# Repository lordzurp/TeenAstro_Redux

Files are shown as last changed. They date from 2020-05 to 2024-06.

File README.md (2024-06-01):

# TeenAstro Redux Project
#### a mini version of the TeenAstro mini version
=========================

## Project moved !
please visit my new repo : [zUrp Astronomics/Unicorn](https://github.com/zUrp-Astronomics/unicorn)

## License
GPL v3

## Author
lordzurp
based on great work of [Charles Lemaire](https://github.com/charleslemaire0/TeenAstro) and [Howard Dutton](http://www.stellarjourney.com) (and a lot of contributors)

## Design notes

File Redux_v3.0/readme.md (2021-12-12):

# TeenAstro Redux Project

#### A mini version of the TeenAstro mini

[][release]
[][license] 

[release]: https://github.com/lordzurp/TeenAstro_Redux/releases
[license]: https://raw.githubusercontent.com/lordzurp/TeenAstro_Redux/master/LICENSE

===========================

## Redux 3.0 — the Finale Edition

### Pre-release notes

> The board isn’t validated yet, please don’t build it right now! Also, the firmware isn’t final neither.

===========================

This version is a mix between the main board and the mini board. The idea is to have a (very) small board that can easily integrate with mounts while still retaining the extended functions of the main unit.

## Source files
[EasyEDA](https://oshwlab.com/lordzurp/teenastro-redux_v3)

## 3D view

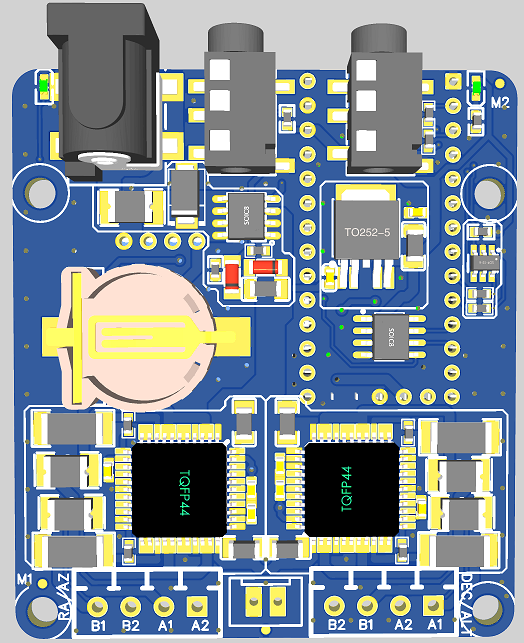
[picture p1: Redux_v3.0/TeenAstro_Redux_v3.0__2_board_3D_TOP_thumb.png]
3D_top

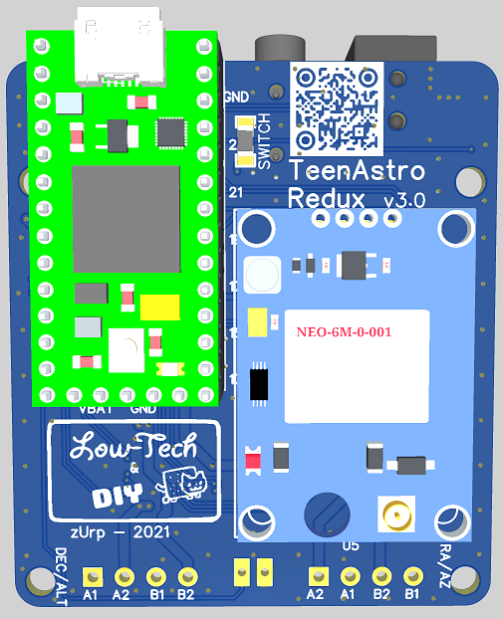
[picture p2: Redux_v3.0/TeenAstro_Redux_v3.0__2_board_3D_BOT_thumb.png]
3D_bot


## Schematics

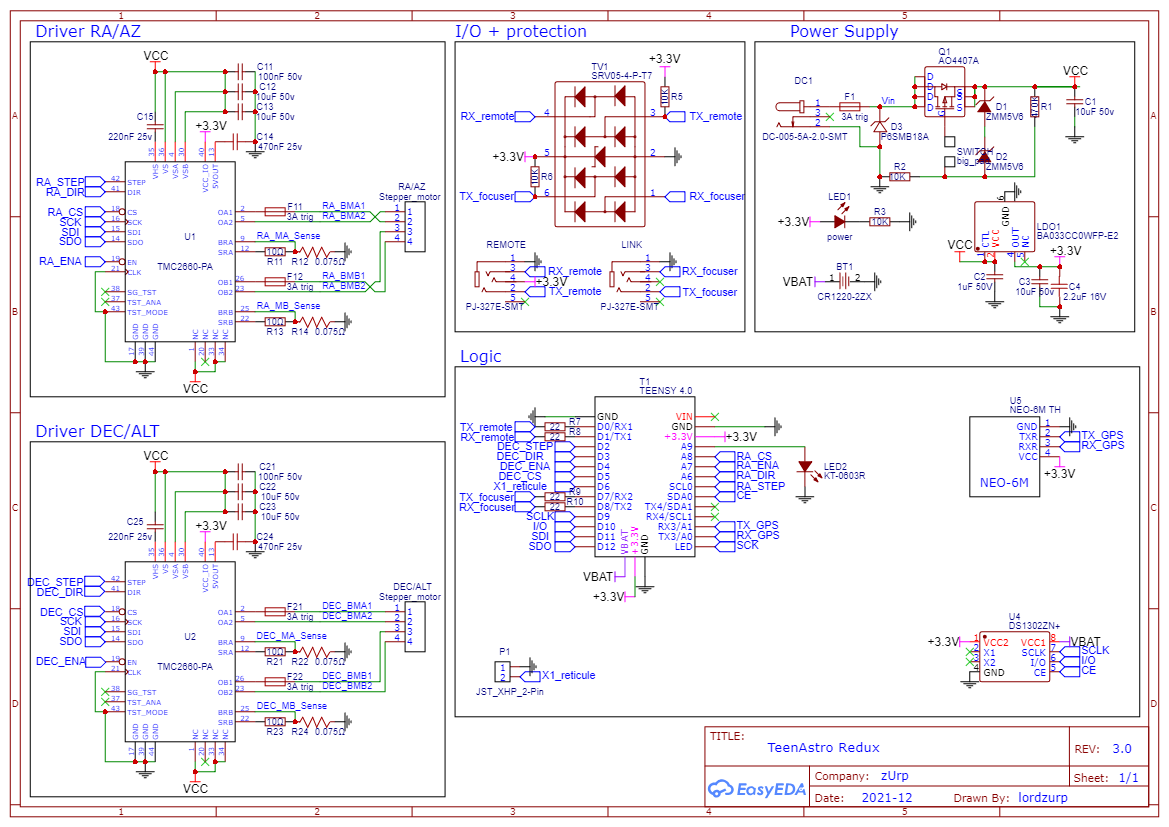
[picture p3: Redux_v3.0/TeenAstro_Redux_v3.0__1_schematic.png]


## Evolution from the v2.4 series

### Teensy 4.0
The (not so) new Teensy 4.0 is a beast of computing power, with a 600 MHz Cortex-M7 CPU. It is almost pin-to-pin compatible with the Teensy 3.2, except for the UART.

The main difference is that the 4.0 **isn’t 5 V compliant**, the logic voltage is 3.3 V across the board and the SHC.

The board’s routing was updated to comply with the constraints of the new form factor. As a consequence, specific firmware is needed, with branch 3.0 (under development).

### Integrated Stepper Driver
To minimize the assembling complexity of the unit, the motor drivers are soldered directly to the board. This makes for more reliable connections and easier production.

The chosen drivers are the **TMC2660**.

They include all the benefits and internal functions of the TMC5160, but with integrated MOSfet which is capable of driving the 3A max stepper motors and is protected by resetting fuses.

### Onboard GPS
There is a space on the board to solder a GPS module.

Depending on the casing, you may need an external antenna (if there’s not enough place inside, or if the casing is made of metal which would reduce the gain of the antenna).

### Focuser
**Awaiting software development**

The board can be used either to control the mount or the focuser or the derotator. The onboard additional chip (DS1302) can be used by the focuser’s firmware and ignored by the main firmware.

A link port allows connecting the two boards and it also provides unified controls with a crossover cable. The use depends on which firmware is uploaded to the board.

### Reworked Power Supply
The power input is protected from polarity inversion, ESD and short-circuiting by a resetting 3A fuse.

The ON/OFF switch is now a logic-level switch, it doesn’t have to support the full-board current. Any regular switch will do the job. Two pads are added for soldering the wires and one can short-circuit them if there is no need for a power-off switch.

The logic voltage is **3.3 V**, as per the Teensy 4.0 requirements (see below).

The button battery is now a CR1220 (standard CR2032 is far too big).

### Protected I/O
The SHC port and the link port are ESD-protected, so you can plug them while the board is ON (although this isn’t recommended…).

### Removed Features
*	no ST4 port anymore: since the mount guiding requires a computer, having only the USB_link option shouldn’t be a problem.

## Firmware and software update needed (WiP)
*	new pinout
*	TMC2660 support
*	Uploader and Config tool, to support new branch
*	additional motor on the focuser: can be used for a secondary focuser or derotator. Some code is available in OnStep, need to review and merge
*	INDI driver: unified control of mount and focuser with a single USB link

## Production Notes
**Follows JLCpcb Capabilities**

*	2-layer board
*	Min track width: 0.2 mm
*	Min clearance: 0.2 mm
*	Via size: 0.25/0.5 mm

#### SMD parts
The whole SMD parts are sourced from the JLCpcb assembly list, so you can order a fully SMD-assembled board.

#### Additional parts
*	Teensy 4.0
*	GPS module (neo-6 compatible)
*	Motor connectors (4 ways pitch 3.5 mm or wires)
*	ON/OFF switch (optional)
*	Reticule connector (optional)

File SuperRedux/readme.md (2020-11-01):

# TeenAstro Redux Project
#### a mini version of the TeenAstro mini version
===========================

## SuperRedux 2.5 - the Small One

### Production notes

**Follow JLCpcb capabilities**

* 4-layers board
* Min track width : 0.15mm
* Min clearence : 0.13mm
* Via size : 0.25/0.5mm

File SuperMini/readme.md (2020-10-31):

## Production notes

**Follow JLCpcb capabilities**

* double-layer board
* Min track width : 0.2mm
* Min clearence : 0.15mm
* Via size : 0.25/0.5mm

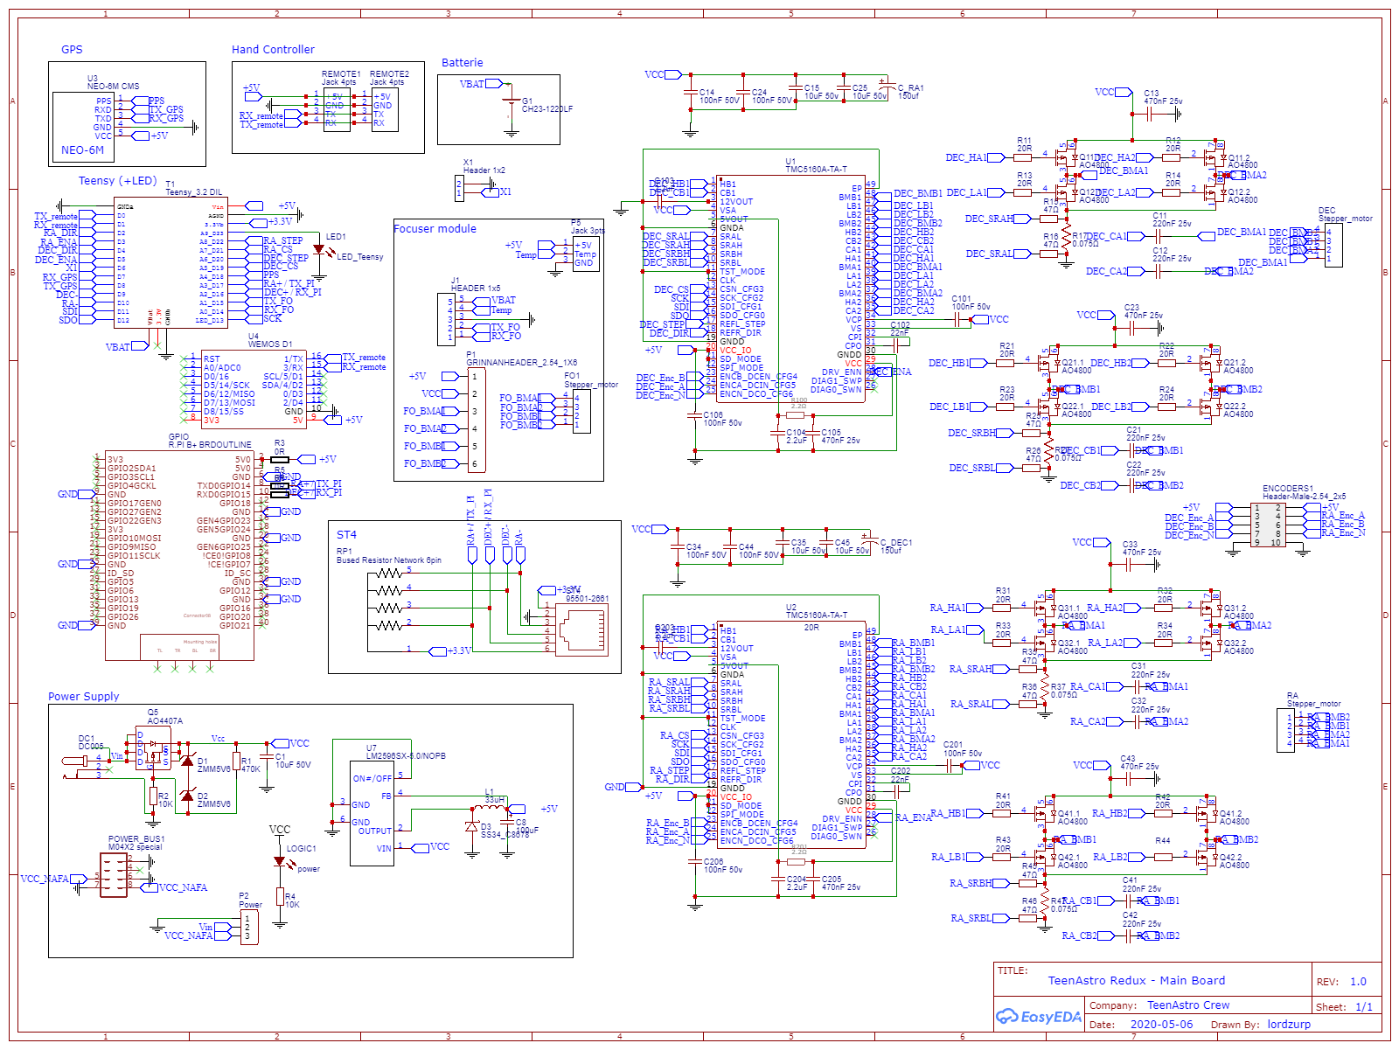
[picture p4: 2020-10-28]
Schematic_TeenAstro SuperMini - PI Edition copy +5v_2020-10-26_22-45-55.png

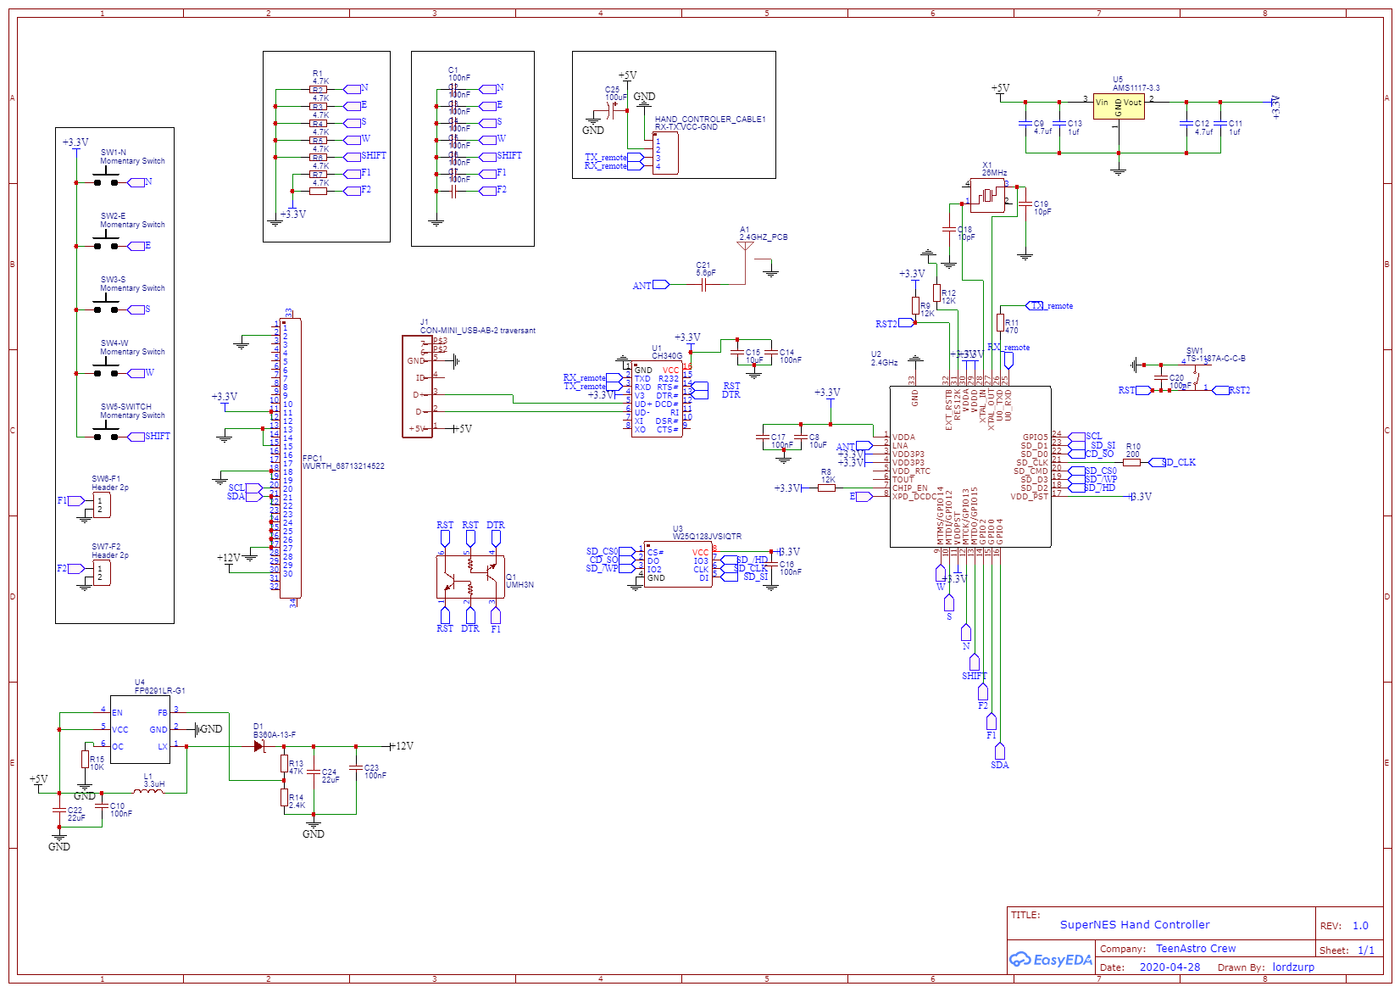
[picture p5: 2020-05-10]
Schematics/Hand_controller.png

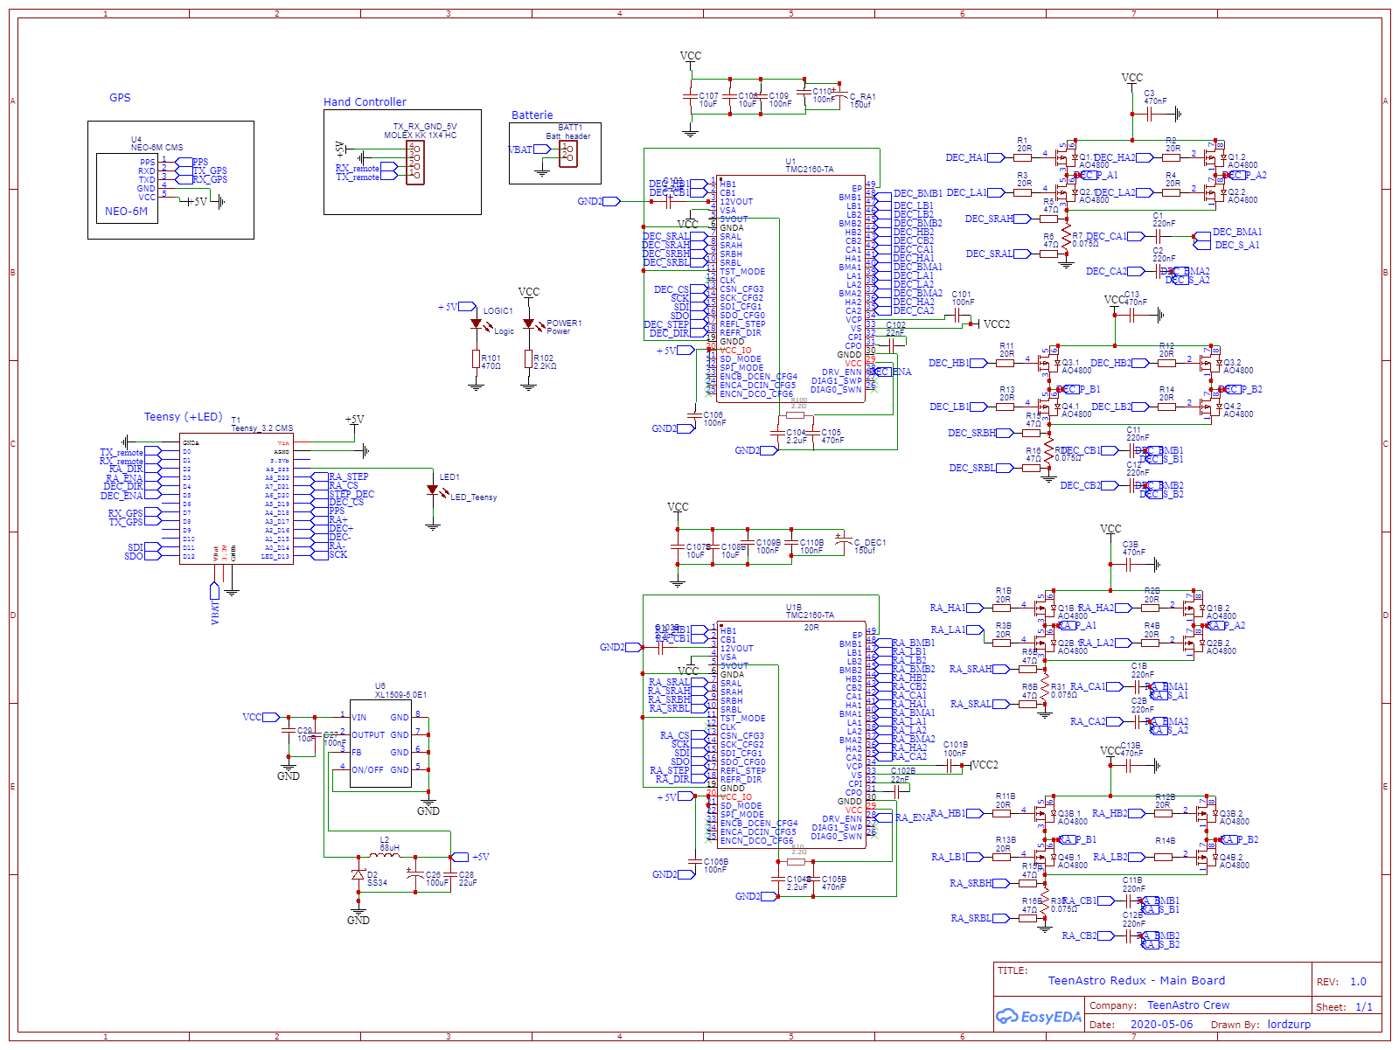
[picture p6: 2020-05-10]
Schematics/Main_board.png

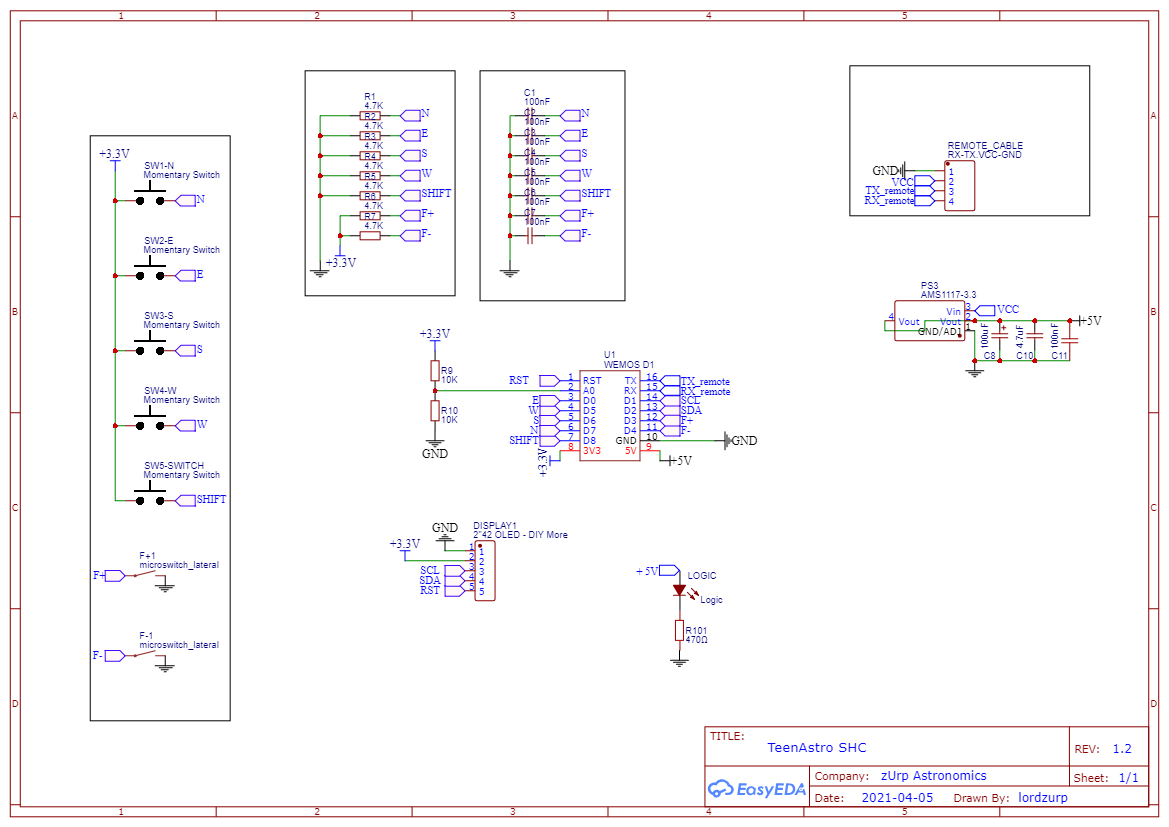
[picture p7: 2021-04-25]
hand controller/TeenAstro SHC - 1_schematic.png

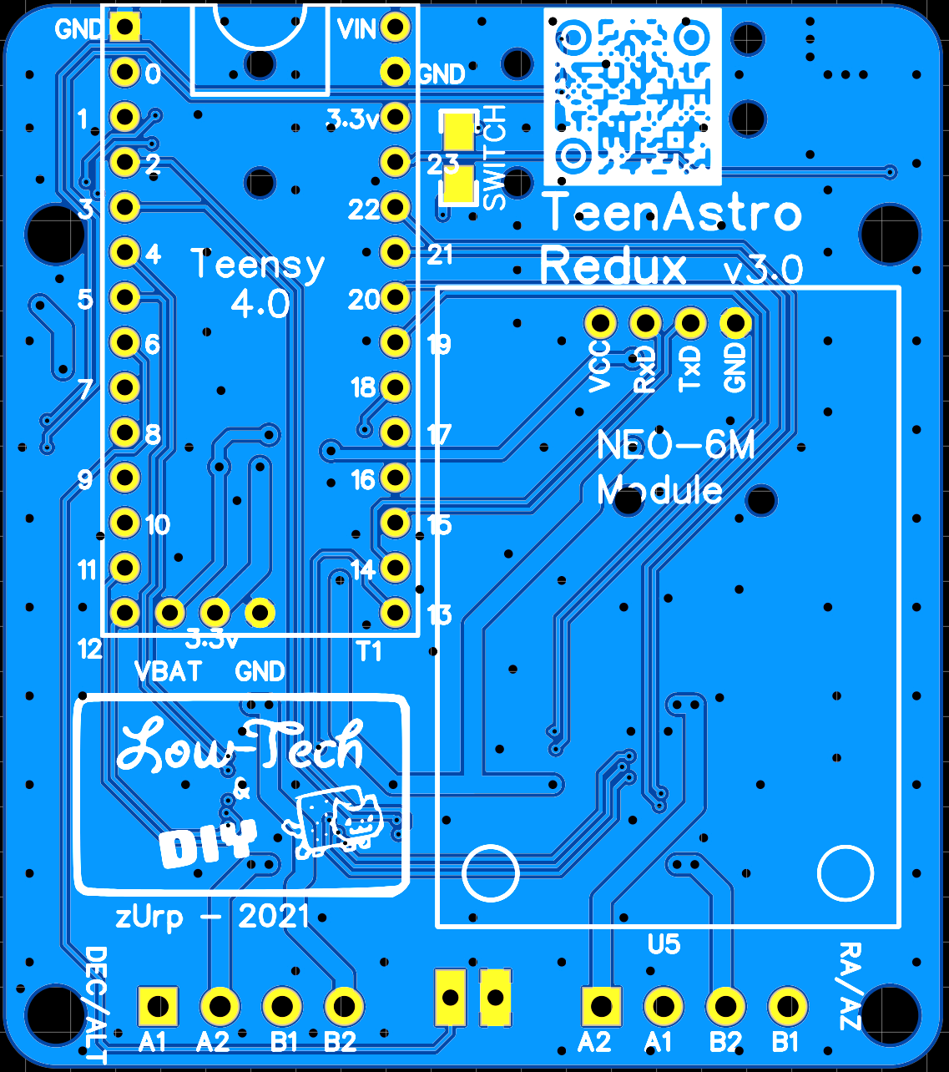
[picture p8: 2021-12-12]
Redux_v3.0/TeenAstro_Redux_v3.0__2_board_BOT.png

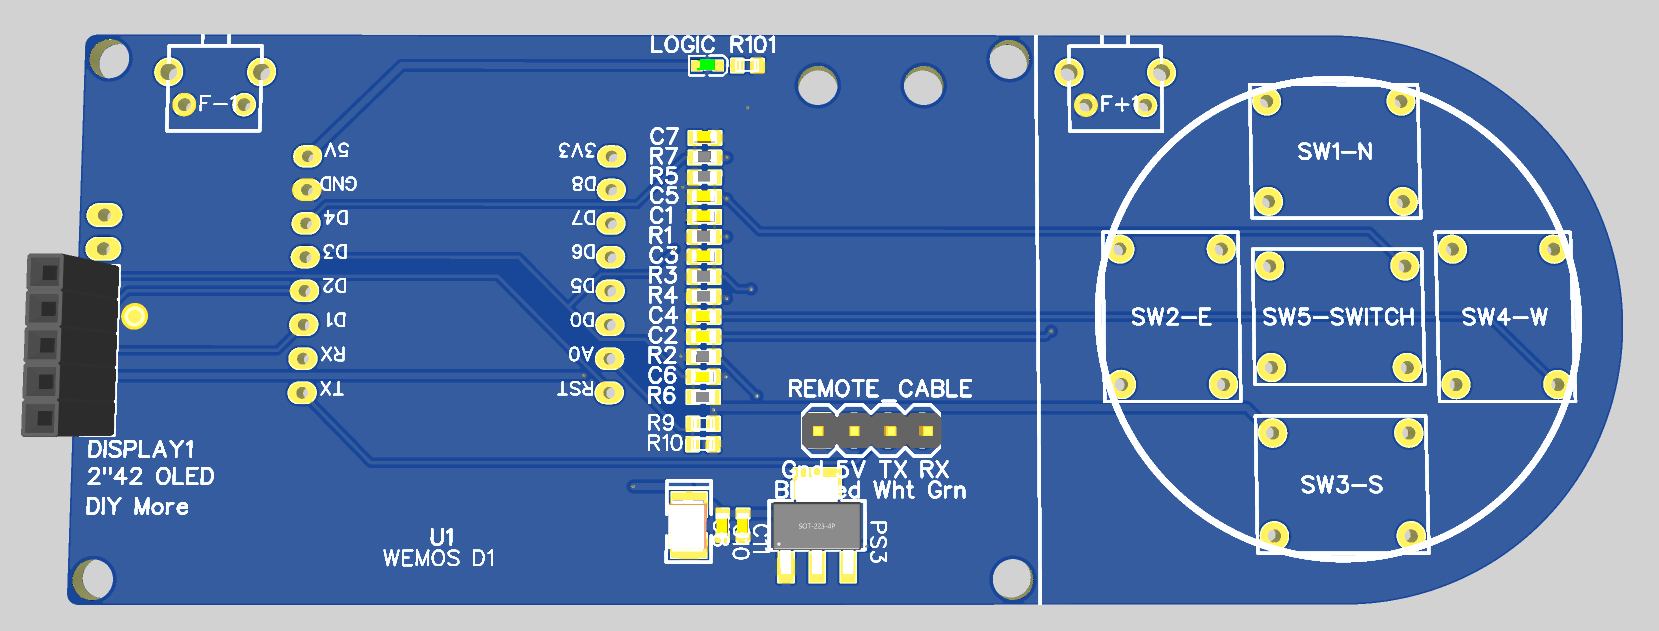
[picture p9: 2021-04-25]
hand controller/TeenAstro SHC - 2_3D-view.png

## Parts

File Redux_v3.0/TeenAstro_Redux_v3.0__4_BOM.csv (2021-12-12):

ID | Name | Designator | Footprint | Quantity | Manufacturer Part | Manufacturer | Supplier | Supplier Part | Price
1 | CR1220-2ZX | BT1 | BAT-SMD_CR1220-2ZX | 1 | CR1220-2ZX | Q&J | LCSC | C969906 | 0.283
2 | 10uF 50v | C1,C3,C12,C13,C22,C23 | C1206 | 6 | CL31A106KBHNNNE | SAMSUNG | LCSC | C13585 | 0.033
3 | 1uF 50V | C2 | C0603 | 1 | CL10A105KB8NNNC | SAMSUNG | LCSC | C15849 | 0.005
4 | 2.2uF 16V | C4 | C_0603 | 1 | CL10A225KO8NNNC | SAMSUNG | LCSC | C23630 | 0.006
5 | 100nF 50v | C11,C21 | C_0603 | 2 | CC0603KRX7R9BB104 | YAGEO | LCSC | C14663 | 0.002
6 | 470nF 25v | C14,C24 | C_0603 | 2 | CL10B474KA8NNNC | SAMSUNG | LCSC | C1623 | 0.007
7 | 220nF 25v | C15,C25 | C_0603 | 2 | CL10B224KA8NNNC | SAMSUNG | LCSC | C21120 | 0.006
8 | ZMM5V6 | D1,D2 | LL-34_L3.5-W1.5-RD | 2 | ZMM5V6 | SEMTECH | LCSC | C8062 | 0.017
9 | P6SMB18A | D3 | SMB_L4.6-W3.6-LS5.3-RD | 1 | P6SMB18A | Formosa Microsemi | LCSC | C286254 | 0.056
10 | DC-005-5A-2.0-SMT | DC1 | DC-IN-TH_DC-005-5A-2.0-SMT | 1 | DC-005-5A-2.0-SMT | XKB Enterprise | LCSC | C319134 | 0.177
11 | Stepper_motor | DEC/ALT,RA/AZ | STEPPER_MOTOR_VERT | 2 | 1x4 pin header
12 | 3A trig | F1,F11,F12,F21,F22 | F1812 | 5 | SMD1812P300SLR/24 | PTTC(Polytronics Tech) | LCSC | C495359 | 0.464
13 | BA033CC0WFP-E2 | LDO1 | TO-252-5_L6.5-W5.5-P1.30-LS10.0-BR | 1 | BA033CC0WFP-E2 | ROHM | LCSC | C84986 | 0.808
14 | power | LED1 | LED0603-R-RD | 1 | 19-217/GHC-YR1S2/3T | EVERLIGHT | LCSC | C72043 | 0.027
15 | KT-0603R | LED2 | LED0603-R-RD | 1 | KT-0603R | KENTO | LCSC | C2286 | 0.005
16 | PJ-327E-SMT | LINK,REMOTE | AUDIO-SMD_PJ-327E-SMT | 2 | PJ-327E-SMT | XKB Enterprise | LCSC | C319105 | 0.118
17 | JST_XHP_2-Pin | P1 | JST-XHP2 | 1
18 | AO4407A | Q1 | SOIC-8_L4.9-W3.9-P1.27-LS6.0-BL | 1 | AO4407A | AOS | LCSC | C2841482 | 0.199
19 | 470K | R1 | R0603 | 1 | 0603WAF4703T5E | UniOhm | LCSC | C23178 | 0.001
20 | 10K | R2,R3,R5,R6 | R0603 | 4 | 0603WAF1002T5E | UniOhm | LCSC | C25804 | 0.001
21 | 22 | R7,R8,R9,R10 | R0603 | 4 | 0603WAF220JT5E | UniOhm | LCSC | C23345 | 0.001
22 | 10Ω | R11,R13,R21,R23 | R0603 | 4 | 0603WAF100JT5E | UniOhm | LCSC | C22859 | 0.001
23 | 0.075Ω | R12,R14,R22,R24 | R2512 | 4 | MS123WF750MT4E | Uniroyal Elec | LCSC | C78195 | 0.126
24 | big_pad | SWITCH | BIG_PAD | 1 |  |  | PJRC
25 | TEENSY 4.0 | T1 | TEENSY 4.0 DIL | 1 | Teensy 4.0 | PJRC
26 | SRV05-4-P-T7 | TV1 | SOT-23-6_L2.9-W1.6-P0.95-LS2.8-BR | 1 | SRV05-4-P-T7 | PROTEK | LCSC | C85364 | 0.125
27 | TMC2660-PA | U1,U2 | PQFP44_WITH_PADS | 2 | TMC2660-PA-T | Trinamic | LCSC | C915852 | 9.548
28 | DS1302ZN+ | U4 | SOIC-8_L4.9-W3.9-P1.27-LS6.0-BL | 1 | DS1302Z+T&R | MAXIM | LCSC | C8959 | 4.07
29 | NEO-6M TH | U5 | NEO-6M-GPS TH | 1 | NEO-6M |  | PJRC

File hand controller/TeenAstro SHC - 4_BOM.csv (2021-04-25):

ID | Name | Designator | Footprint | Quantity | Manufacturer Part | Manufacturer | Supplier | Supplier Part | Price | LCSC Assembly | JLCPCB SMD | Paste Type
1 | 100nF | C1,C2,C3,C4,C5,C6,C7,C11 | C_0603 | 8 | CC0603KRX7R9BB104 | YAGEO | LCSC | C14663 | 0.0034 | Yes
2 | 100uF | C8 | CAP-SMD_L3.5-W2.8 | 1 | TAJB107K006RNJ | AVX | LCSC | C16133 | 0.1544 | Yes | Yes | base
3 | 4.7uF | C10 | C_0603 | 1 | CL10A475KO8NNNC | SAMSUNG | LCSC | C19666 | 0.0132 |  | Yes
4 | 2"42 OLED - DIY More | DISPLAY1 | HDR-TH_5P-P2.54-V | 1 | 2.54mm 1*5P Header | ReliaPro | LCSC | C50951 | 0.0161
5 | microswitch_lateral | F+1,F-1 | MICROSWITCH_LATERAL | 2
6 | Logic | LOGIC | LED0603-RD | 1 | 19-217/GHC-YR1S2/3T | EVERLIGHT | LCSC | C72043 | 0.0246 | Yes
7 | AMS1117-3.3 | PS3 | SOT-223-3_L6.5-W3.4-P2.30-LS7.0-BR | 1 | AMS1117-3.3 | AMS | LCSC | C6186 | 0.0998 | Yes | Yes | base
8 | 4.7K | R1,R2,R3,R4,R5,R6,R7 | R_0603 | 7 | 0603WAF4701T5E | UniOhm | LCSC | C23162 | 0.0012 | Yes
9 | 10K | R9,R10 | R_0603 | 2 | 0603WAF1002T5E | UniOhm | LCSC | C25804 | 0.001 | Yes | Yes | base
10 | 470Ω | R101 | R_0603 | 1 | 0603WAF4700T5E | UniOhm | LCSC | C23179 | 0.0014 | Yes
11 | RX-TX.VCC-GND | REMOTE_CABLE | HDR-TH_4P-P2.54-V_LARGE | 1 | 210S-1*4P L=11.6MMGold-plated black | Ckmtw | LCSC | C124378 | 0.0261 | Yes |  | expand
12 | Momentary Switch | SW1-N,SW2-E,SW3-S,SW4-W,SW5-SWITCH | SWITCH_NAVI | 5 | TL3300CF260Q | E-SWITCH | Mouser | 612-TL3300CF260Q
13 | WEMOS D1 | U1 | WEMOS D1 MINI | 1

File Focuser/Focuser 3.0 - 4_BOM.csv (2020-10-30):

ID | Name | Designator | Footprint | Quantity | Manufacturer Part | Manufacturer | Supplier | Supplier Part | LCSC Assembly
1 | Momentary Switch | SW1-N,SW5-SWITCH,SW4-W,SW3-S,SW2-E | SWITCH_NAVI | 5 | TL3300CF260Q | E-SWITCH | Mouser | 612-TL3300CF260Q
2 | Header 2p | SW7-F2,SW6-F1 | HDR-TH_2P-P2.54-V-M | 2 | 2.54-1*2PFemale | BOOMELE | LCSC | C49661
3 | 4.7K | R5,R6,R1,R2,R3,R4,R7 | R_0603 | 7 | 0603WAF4701T5E | UniOhm | LCSC | C23162 | Yes
4 | 470Ω | R101 | R_0603 | 1 | 0603WAF4700T5E | UniOhm | LCSC | C23179 | Yes
5 | 100nF | C6,C5,C4,C3,C2,C1,C7 | C_0603 | 7 | CC0603KRX7R9BB104 | YAGEO | LCSC | C14663 | Yes
6 | 2.54mm 1*5P Header | P1 | HDR-TH_5P-P2.54-V | 1 | 2.54mm 1*5P Header | ReliaPro | LCSC | C50951
7 | Logic | LOGIC1 | LED0603-RD | 1 | 19-217/GHC-YR1S2/3T | EVERLIGHT | LCSC | C72043 | Yes
8 | RX-TX.VCC-GND | HAND_CONTROLER_CABLE1 | 210S-1X4P | 1 | 210S-1*4P L=11.6MMGold-plated black | Ckmtw | LCSC | C124378
9 | WEMOS D1 | U2 | WEMOS D1 MINI | 1
10 | 100uF | C9 | CAP-SMD_L3.5-W2.8-R-RD | 1 | TAJB107K006RNJ | AVX | LCSC | C16133 | Yes

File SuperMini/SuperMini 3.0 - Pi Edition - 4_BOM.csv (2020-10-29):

ID | Name | Designator | Footprint | Quantity | Manufacturer Part | Manufacturer | Supplier | Supplier Part | LCSC Assembly | Mounted | EasyEDA
1 | 2.2Ω | R100,R201 | R_0603 | 2 | 0603WAF220KT5E | UniOhm | LCSC | C22939
2 | 0.075Ω | R47,R37,R27,R17 | R2512 | 4 | MS123WF750MT4E | Uniroyal Elec | LCSC | C78195
3 | SS34_C8678 | D3 | DO-214AC_L4.3-W2.7-LS5.3-RD | 1 | SS34 | MDD | LCSC | C8678 | Yes
4 | 33uH | L1 | IND-SMD_L7.1-W6.6_YXMAA0603 | 1 | MWSA0603-330MT | Sunlord | LCSC | C132138 | Yes
5 | M04X2 special | POWER_BUS1 | HDR-M-2.54_2X4 SPECIAL | 1
6 | ZMM5V6 | D1,D2 | LL-34_L3.5-W1.5-RD | 2 | ZMM5V6 | SEMTECH | LCSC | C8062 | Yes
7 | Teensy_3.2 DIL | T1 | TEENSY 4.0 DIL | 1 | Teensy 3.2 |  | PJRC | TEENSY32 |  | Yes
8 | WEMOS D1 | U4 | WEMOS_D1_MINI_LIGHT | 1
9 | NEO-6M CMS | U3 | GPS NEO-6M | 1 | NEO-6M |  | PJRC
10 | 470K | R1 | R0805 | 1 | 0805W8F4703T5E | UniOhm | LCSC | C17709 | Yes
11 | LM2596SX-5.0/NOPB | U7 | TO-263-5_L10.2-W9.9-P1.70-LS14.4-TL | 1 | LM2596SX-5.0/NOPB | TI | LCSC | C10002 | Yes
12 | CH23-1220LF | G1 | CH23-1220LF | 1
13 | Header 2.54 1X6 | P1 | HEADER_2.54_1X6_PCB | 1 | Header-Male-2.54_1x6 | BOOMELE |  | C37208
14 | AO4407A | Q9 | SOIC-8_L4.9-W3.9-P1.27-LS6.0-BL | 1 | AO4407A | AOS | LCSC | C16072 | Yes
15 | 22nF | C202,C102 | C_0603 | 2 | CL10B223KB8NNNC | SAMSUNG | LCSC | C21122 | Yes
16 | Jack 3pts | P5 | JACK_3.5_3PTS | 1 | Molex_4x1
17 | 100nF 50V | C14,C34,C44,C24 | C0603 | 4 | CC0603KRX7R9BB104 | YAGEO | LCSC | C14663 | Yes
18 | power | LOGIC1 | LED0603-RD | 1 | 19-217/GHC-YR1S2/3T | EVERLIGHT | LCSC | C72043 | Yes
19 | LED_Teensy | LED1 | LED0603-RD | 1 | 19-217/GHC-YR1S2/3T | EVERLIGHT | LCSC | C72043 | Yes
20 | 0R | R5,R6,R3 | R0805_SHORT | 3
21 | Bused Resistor Network 6pin | RP1 | RESSIP-5 | 1 | Bused Resistor Network 6pin
22 | 95501-2661 | ST4 | 85503-5001 | 1 | 95501-2661 | MOLEX | LCSC | C240856
23 | 470nF 25v | C33,C205,C23,C13,C105,C43 | C_0603 | 6 | CL10B474KA8NNNC | SAMSUNG | LCSC | C1623 | Yes
24 | 150uf | C_DEC1,C_RA1 | 100UF/25V | 2 | ?
25 | 10uF 50v | C15,C25,C35,C45 | C1206 | 4 | CL31A106KBHNNNE | SAMSUNG | LCSC | C13585 | Yes
26 | 10uF 50V | C1 | C1206 | 1 | CL31A106KBHNNNE | SAMSUNG | LCSC | C13585 | Yes
27 | DC005 | DC1 | DC-IN-TH_DC-005-5A-2.0 | 1 | - | Made in China | LCSC | C9738
28 | TMC5160A-TA-T | U2,U1 | TQFP-48_L7.0-W7.0-P0.50-LS9.0-BL-EP | 2 | TMC2160-TA-T | TRINAMIC Motion Control GmbH | LCSC | C465948 | Yes
29 | Stepper_motor | DEC1,RA1,FO1 | STEPPER_MOTOR | 3 | 1x4 pin header
30 | 10K | R4 | R0603 | 1 | 0603WAF1002T5E | UniOhm | LCSC | C25804 | Yes
31 | SMD1812P300SLR/24 | F4,F3,F2,F1,F6,F5 | F1812 | 6 | SMD1812P300SLR/24 | PTTC(Polytronics Tech) | LCSC | C495359 | Yes
32 | 100uF | C8 | CAP-SMD_L3.5-W2.8-R-RD | 1 | TAJB107K006RNJ | AVX | LCSC | C16133 | Yes
33 | HEADER 1x5 | J1 | 1X5-2.54MM-HEADER | 1
34 | Power | P2 | HDR-TH_3P-P2.54-V | 1 | Header-Female-2.54_1x3 | Boom Precision Elec | LCSC | C146243
35 | 2.2uF | C103,C104,C204,C203 | C_0603 | 4 | CL10A225KO8NNNC | SAMSUNG | LCSC | C23630 | Yes
36 | Header 1x2 | X1 | HEADER 1X2 | 1
37 | 100nF 50v | C206,C101,C201,C106 | C_0603 | 4 | CC0603KRX7R9BB104 | YAGEO | LCSC | C14663 | Yes
38 | 10K | R2 | R0805 | 1 | 0805W8F1002T5E | UniOhm | LCSC | C17414 | Yes
39 | R.PI B+ BRDOUTLINE | GPIO1 | RASPBERRY PI 3 B+ | 1
40 | 47Ω | R46,R45,R25,R26,R16,R35,R15,R36 | R_0603 | 8 | 0603WAF470JT5E | UniOhm | LCSC | C23182 | Yes
41 | 220nF 25v | C42,C41,C32,C31,C22,C21,C11,C12 | C_0603 | 8 | CL10B224KA8NNNC | SAMSUNG | LCSC | C21120 | Yes
42 | 20R | R31,R43,R41,R14,R24,R11,R22,R21,R33,R32,R34,R44,R42,R23,R13,R12 | R_0603 | 16 | 0603WAF200JT5E | UniOhm | LCSC | C22950 | Yes
43 | Jack 4pts | REMOTE2,REMOTE1 | JACK_3.5_4PTS | 2 | Molex_4x1
44 | Header-Male-2.54_2x5 | ENCODERS1 | HDR-5X2/2.54 | 1 | Header-Male-2.54_2x5 | EasyEDA | EasyEDA | E28207 |  |  | E28207
45 | AO4800 | Q8,Q4,Q7,Q1,Q2,Q3,Q5,Q6,Q32,Q11,Q12,Q41,Q42,Q31,Q22,Q21 | SOIC-8_L4.9-W3.9-P1.27-LS6.0-BL | 16 | AO4800 | AOS | LCSC | C17098

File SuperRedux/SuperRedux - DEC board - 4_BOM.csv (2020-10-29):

ID | Name | Designator | Footprint | Quantity | Manufacturer Part | Manufacturer | Supplier | Supplier Part | Mounted | LCSC Assembly
1 | 2.2Ω | R201 | R_0603 | 1 | 0603WAF220KT5E | UniOhm | LCSC | C22939
2 | 0.075Ω | R47,R37 | R2512 | 2 | MS123WF750MT4E | Uniroyal Elec | LCSC | C78195
3 | Teensy_3.2 CMS | T1 | TEENSY 3.2 DIL | 1 | Teensy 3.2 |  | PJRC | TEENSY32 | Yes
4 | 22nF | C202 | C_0603 | 1 | CL10B223KB8NNNC | SAMSUNG | LCSC | C21122 |  | Yes
5 | 100nF 50V | C44,C34 | C0603 | 2 | CC0603KRX7R9BB104 | YAGEO | LCSC | C14663 |  | Yes
6 | Header_1x4 | POWERBUS | HDR-TH_4P-P2.54-V | 1 | 210S-1*4P L=11.6MMGold-plated black | Ckmtw | LCSC | C124378
7 | 470nF 25v | C205,C33,C43 | C_0603 | 3 | CL10B474KA8NNNC | SAMSUNG | LCSC | C1623 |  | Yes
8 | 150uf | C1 | CAP-6.3*12 HORIZONTAL | 1 | ?
9 | 10uF 50v | C35,C45 | C1206 | 2 | CL31A106KBHNNNE | SAMSUNG | LCSC | C13585 |  | Yes
10 | TMC5160A-TA-T | U2 | TQFP-48_L7.0-W7.0-P0.50-LS9.0-BL-EP | 1 | TMC2160-TA-T | TRINAMIC Motion Control GmbH | LCSC | C465948 |  | Yes
11 | Stepper_motor | RA | STEPPER_MOTOR | 1 | 1x4 pin header
12 | SMD1812P300SLR/24 | F2,F1 | F1812 | 2 | SMD1812P300SLR/24 | PTTC(Polytronics Tech) | LCSC | C495359 |  | Yes
13 | 2.2uF | C204,C203 | C_0603 | 2 | CL10A225KO8NNNC | SAMSUNG | LCSC | C23630 |  | Yes
14 | 100nF 50v | C201,C206 | C_0603 | 2 | CC0603KRX7R9BB104 | YAGEO | LCSC | C14663 |  | Yes
15 | 47Ω | R45,R35,R46,R36 | R_0603 | 4 | 0603WAF470JT5E | UniOhm | LCSC | C23182 |  | Yes
16 | 220nF 25v | C31,C32,C41,C42 | C_0603 | 4 | CL10B224KA8NNNC | SAMSUNG | LCSC | C21120 |  | Yes
17 | 20R | R42,R41,R31,R33,R32,R44,R43,R34 | R_0603 | 8 | 0603WAF200JT5E | UniOhm | LCSC | C22950 |  | Yes
18 | AO4800 | Q31,Q41,Q32,Q42 | SOIC-8_L4.9-W3.9-P1.27-LS6.0-BL | 4 | AO4800 | AOS | LCSC | C17098

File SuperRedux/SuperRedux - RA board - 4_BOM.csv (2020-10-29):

ID | Name | Designator | Footprint | Quantity | Manufacturer Part | Manufacturer | Supplier | Supplier Part | Mounted | LCSC Assembly
1 | 2.2Ω | R201 | R_0603 | 1 | 0603WAF220KT5E | UniOhm | LCSC | C22939
2 | 0.075Ω | R47,R37 | R2512 | 2 | MS123WF750MT4E | Uniroyal Elec | LCSC | C78195
3 | Teensy_3.2 CMS | T1 | TEENSY 3.2 DIL | 1 | Teensy 3.2 |  | PJRC | TEENSY32 | Yes
4 | 22nF | C202 | C_0603 | 1 | CL10B223KB8NNNC | SAMSUNG | LCSC | C21122 |  | Yes
5 | 100nF 50V | C34,C44 | C0603 | 2 | CC0603KRX7R9BB104 | YAGEO | LCSC | C14663 |  | Yes
6 | Header_1x4 | POWERBUS1 | HDR-TH_4P-P2.54-V | 1 | 210S-1*4P L=11.6MMGold-plated black | Ckmtw | LCSC | C124378
7 | 470nF 25v | C33,C205,C43 | C_0603 | 3 | CL10B474KA8NNNC | SAMSUNG | LCSC | C1623 |  | Yes
8 | 150uf | C1 | CAP-6.3*12 HORIZONTAL | 1 | ?
9 | 10uF 50v | C45,C35 | C1206 | 2 | CL31A106KBHNNNE | SAMSUNG | LCSC | C13585 |  | Yes
10 | TMC5160A-TA-T | U2 | TQFP-48_L7.0-W7.0-P0.50-LS9.0-BL-EP | 1 | TMC2160-TA-T | TRINAMIC Motion Control GmbH | LCSC | C465948 |  | Yes
11 | Stepper_motor | RA1 | STEPPER_MOTOR | 1 | 1x4 pin header
12 | SMD1812P300SLR/24 | F1,F2 | F1812 | 2 | SMD1812P300SLR/24 | PTTC(Polytronics Tech) | LCSC | C495359 |  | Yes
13 | 2.2uF | C203,C204 | C_0603 | 2 | CL10A225KO8NNNC | SAMSUNG | LCSC | C23630 |  | Yes
14 | 100nF 50v | C201,C206 | C_0603 | 2 | CC0603KRX7R9BB104 | YAGEO | LCSC | C14663 |  | Yes
15 | CR2032-BS-5-1 | B1 | BAT-TH_CR2032-BS-5-1 | 1 | CR2032-BS-5-1 | Q&J | LCSC | C70379
16 | 47Ω | R35,R36,R46,R45 | R_0603 | 4 | 0603WAF470JT5E | UniOhm | LCSC | C23182 |  | Yes
17 | 220nF 25v | C32,C31,C41,C42 | C_0603 | 4 | CL10B224KA8NNNC | SAMSUNG | LCSC | C21120 |  | Yes
18 | 20R | R42,R33,R31,R32,R44,R41,R43,R34 | R_0603 | 8 | 0603WAF200JT5E | UniOhm | LCSC | C22950 |  | Yes
19 | AO4800 | Q41,Q42,Q32,Q31 | SOIC-8_L4.9-W3.9-P1.27-LS6.0-BL | 4 | AO4800 | AOS | LCSC | C17098

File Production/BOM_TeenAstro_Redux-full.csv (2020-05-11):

ID | Name | Designator | Footprint | Quantity | Manufacturer Part | Manufacturer | Supplier | Supplier Part | 3DModel | link
1 | TEENSY 3.2 CMS | U4 | TEENSY 3.2 CMS | 1 |  |  |  |  | teensy_4
2 | LED-3MM | LED1 | LED-3MM/2.54 | 1
3 | DC005-2.5MM | DC1 | CONN-TH_DC-2.5-5A | 1
4 | TMC5160A-TA-T | U1,U1B | TQFP-48_L7.0-W7.0-P0.50-LS9.0-BL-EP | 2 | TMC5160-TA | TRINAMIC Motion Control GmbH | LCSC | C465956
5 | 220nF 25V | C13,C2,C12,C3,C13B,C2B,C12B,C3B | C_0603 | 8 | CL10B224KA8NNNC | SAMSUNG | LCSC | C21120 | C0603_L1.6-W0.8-H0.8
6 | 100nF 50V | C106,C31,C40,C106B,C39B,C31B,C40B,C39,C1,C511,C510,C509,C5,C6,C7,C10,C508,C17,C19,C21,C24,C505 | C_0603 | 22 | CC0603KRX7R9BB104 | YAGEO | LCSC | C14663 | C0603_L1.6-W0.8-H0.8
7 | 2.2uF 16V | C33,C34,C33B,C34B | C_0603 | 4 | CL10A225KO8NNNC | SAMSUNG | LCSC | C23630 | C0603_L1.6-W0.8-H0.8
8 | 470nF 25V | C35,C35B | C_0603 | 2 | CL10B474KA8NNNC | SAMSUNG | LCSC | C1623 | C0603_L1.6-W0.8-H0.8
9 | 22nF 50V | C32,C32B | C_0603 | 2 | CL10B223KB8NNNC | SAMSUNG | LCSC | C21122 | C0603_L1.6-W0.8-H0.8
10 | 20R | R11,R1,R3,R2,R13,R12,R14,R4,R11B,R1B,R3B,R2B,R13B,R12B,R14B,R4B | R_0603 | 16 | 0603WAF200JT5E | UniOhm | LCSC | C22950 | R0805_L2.0-W1.3-H0.6
11 | 47R | R15,R5,R16,R112,R15B,R6B,R16B,R6 | R_0603 | 8 | 0603WAF470JT5E | UniOhm | LCSC | C23182 | R0805_L2.0-W1.3-H0.6
12 | AO4800 | Q2,Q1,Q3,Q4,Q2B,Q1B,Q3B,Q4B | SOIC-8_L4.9-W3.9-P1.27-LS6.0-BL | 8 | AO4800 | AOS | LCSC | C17098
13 | 2R2 | R31,R31B | R_0603 | 2 | 0603WAF220KT5E | UniOhm | LCSC | C22939 | R0805_L2.0-W1.3-H0.6
14 | JACK_3.5_4PTS | J1 | JACK_3.5_4PTS | 1
15 | CR1220 | BT1 | CR1220 | 1
16 | NEO-6M-GPS CMS | U5 | NEO-6M-GPS CMS | 1 |  |  |  |  | GPS_neo6m_board
17 | 0R075 2W | R7B,R17,R17B,R7 | R2512 | 4 | MS123WF750MT4E | Uniroyal Elec | LCSC | C78195 | R2512_L6.3-W3.2-H0.6 | https://item.szlcsc.com/347967.html
18 | 10uF 50V | C37B,C38,C38B,C37,C514 | C1206 | 5 | CL31A106KBHNNNE | SAMSUNG | LCSC | C13585
19 | 470R | R101,R508,R506 | R_0603 | 3 | 0603WAF4700T5E | UniOhm | LCSC | C23179 | R0805_L2.0-W1.3-H0.6
20 | Logic | L2,L4 | LED0603-RD | 2 | 19-217/GHC-YR1S2/3T | EVERLIGHT | LCSC | C72043
21 | 2.2K | R102,R505 | R_0603 | 2 | 0603WAF2201T5E | UniOhm | LCSC | C4190 | R0805_L2.0-W1.3-H0.6
22 | Power | L1,L3 | LED0603-RD | 2 | KT-0603R | KENTO | LCSC | C2286 | LED0603_Red
23 | 25MHz | X1 | OSC-SMD_4P-L3.2-W2.5-BL | 1 | X322525MOB4SI | YXC | LCSC | C9006
24 | 22uF 25V | C9,C11,C516 | C0805 | 3 | CL21A226MAQNNNE | SAMSUNG | LCSC | C45783
25 | 4.7uF 50V | C507,C15 | C_1206 | 2 | 1206B475K500NT | FH | LCSC | C29823 | C1206_L3.2-W1.6-H1.3
26 | 1uF 50V | C506,C16 | C_0603 | 2 | CL10A105KB8NNNC | SAMSUNG | LCSC | C15849 | C0603_L1.6-W0.8-H0.8
27 | 10uF 25V | C18,C20 | C_0805 | 2 | CL21A106KAYNNNE | SAMSUNG | LCSC | C15850
28 | 12pF | C22,C23 | C_0603 | 2 | CL10C120JB8NNNC | SAMSUNG | LCSC | C38523 | C0603_L1.6-W0.8-H0.8
29 | RX-TX.VCC-GND | GND-+5V-TX-RX | 210S-1X4P | 1
30 | CON-MINI_USB-AB-2 traversant | J2 | MINI-USB MOLEX TRAVERSANT | 1
31 | UMH3N | Q5 | SC-70-6_L2.2-W1.3-P0.65-LS2.1-BR | 1 | UMH3N | CJ | LCSC | C62892
32 | 4.7K | R518,R517,R516,R515,R514,R513,R512 | R_0603 | 7 | 0603WAF4701T5E | UniOhm | LCSC | C23162 | R0603_L1.6-W0.8-H0.5
33 | 10K | R8 | R0603 | 1 | 0603WAF1002T5E | UniOhm | LCSC | C25804
34 | 12K | R9,R10,R507 | R_0603 | 3 | 0603WAF1202T5E | UniOhm | LCSC | C22790 | R0603_L1.6-W0.8-H0.5
35 | 2.4K | R511 | R0603 | 1 | 0603WAF2401T5E | UniOhm | LCSC | C22940
36 | 47K | R510 | R0603 | 1 | 0603WAF4702T5E | UniOhm | LCSC | C25819
37 | 200R | R509 | R_0603 | 1 | 0603WAF2000T5E | UniOhm | LCSC | C8218 | R0603_L1.6-W0.8-H0.5
38 | TS-1187A-C-C-B | SW1 | SW-SMD_4P-L5.1-W5.1-P3.70-LS6.4 | 1 | TS-1187A-C-C-B | XKB Enterprise | LCSC | C318889
39 | Header 2p | SW6-F1,SW7-F2 | HDR-TH_2P-P2.54-V-M | 2
40 | FP6291LR | U2 | SOT-23-6_L2.9-W1.6-P0.95-LS2.8-BR | 1 | FP6291LR-G1 | Feeling Technology | LCSC | C18701
41 | CH340G | U503 | SOIC-16_L9.9-W3.9-P1.27-LS6.0-BL | 1 | CH340G | WCH | LCSC | C14267
42 | W25Q128JVSIQTR | U502 | SOIC-8_L5.3-W5.3-P1.27-LS8.0-BL | 1 | W25Q128JVSIQTR | WINBOND | LCSC | C97521
43 | Momentary Switch | SW1-N,SW2-E,SW3-S,SW4-W,SW5-SWITCH | CARBON-KEY-OBA V1 | 5
44 | AMS1117-3.3 | U7 | SOT-223-3_L6.5-W3.4-P2.30-LS7.0-BR | 1 | AMS1117-3.3 | AMS | LCSC | C6186 | SOT-223-4P_L6.5-W3.5-H1.6-LS7.0-P2.30 | https://item.szlcsc.com/410724.html
45 | WIFI ANTENNA MIFA INVERTED F ANTENNA | ANT_WIFI | WIFI ANTENNA MIFA INVERTED F ANTENNA | 1 |  |  |  |  |  | http://www.ti.com/lit/an/swra117d/swra117d.pdf
46 | 5.6pF | C28 | C0603 | 1 | 0603N5R6C500 | Huaxin S&T | LCSC | C123584 | C0603_L1.6-W0.8-H0.8 | https://item.szlcsc.com/362304.html
47 | ESP8266 | U3 | QFN-32_L5.0-W5.0-P0.50-TL-EP | 1 | ESP8266EX | ESPRESSIF | LCSC | C77967 | QFN-32_L5.0-W5.0-H0.9-P0.50
48 | R0805 0R | R18,R19 | R0805 | 2 |  |  |  |  | R0805_L2.0-W1.3-H0.6 | https://item.szlcsc.com/142685.html
49 | XL1509-5.0E1 | U504 | SOIC-8_L5.0-W4.0-P1.27-LS6.0-BL | 1 | XL1509-5.0E1 | XLSEMI | LCSC | C61063
50 | SS34 | D1,D502 | DO-214AC_L4.3-W2.7-LS5.3-FD | 2 | SS34 | MDD | LCSC | C8678
51 | 68uH 1.5A | L5 | IND-SMD_L12.5-W12.5 | 1 | SWRB1204S-680MT | Sunlord | LCSC | C169399 | SMD-PIND_L12.5-W12.5-H8.0 | https://item.szlcsc.com/421430.html
52 | WURTH_68713214522 | FPC1 | FFC-SMD_32P-P0.50 | 1
53 | 470nF 50V | C14,C4B,C14B,C4 | C0805 | 4 | CL21B474KBFNNNE | SAMSUNG | LCSC | C13967 | C0805_L2.0-W1.3-H1.3 | https://item.szlcsc.com/373011.html
54 | 150uf | C_RA1,C_DEC1 | 100UF/25V | 2 | EEUFM1V151 | Panasonic | Element14 | 1848394
55 | 100uF 6.3V | C517,C518 | CAP-SMD_L3.5-W2.8-R-RD | 2 | TAJB107K006RNJ | AVX | LCSC | C16133 | CASE-B_L3.5-W2.8-H1.9 | https://item.szlcsc.com/19983.html
56 | 3.3uH 3.3A | L503 | IND-SMD_L4.4-W4.2 | 1 | MWSA0402-3R3MT | Sunlord | LCSC | C169185 | IND-SMD_L4.2-W4.4-H2.0 | https://item.szlcsc.com/178588.html

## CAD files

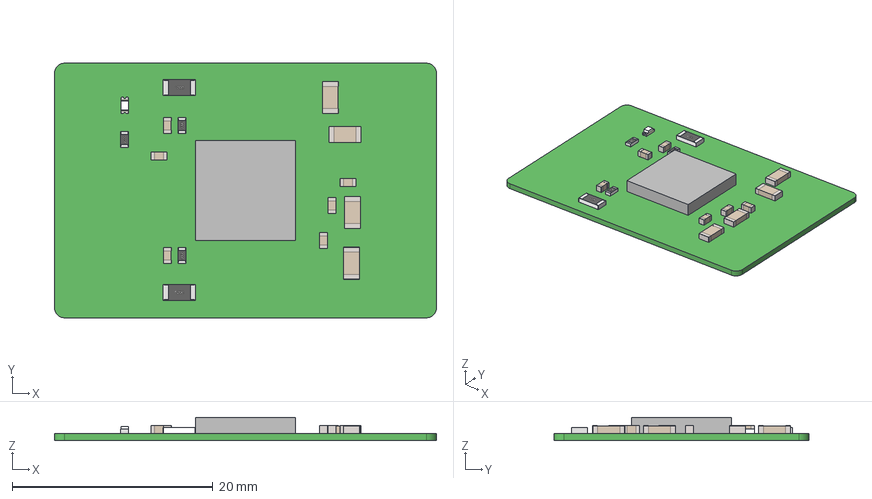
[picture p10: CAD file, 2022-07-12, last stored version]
Datasheets/#6_Stepper_drivers/TMC2660-BOB_3D_Files_Layout_Data_V1.2/3D_TMC2660_BOB_V1.2.step
38.1 x 25.4 x 2.32 mm

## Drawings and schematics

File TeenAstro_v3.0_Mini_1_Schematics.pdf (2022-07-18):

Teensy | GPS

# SHC remote

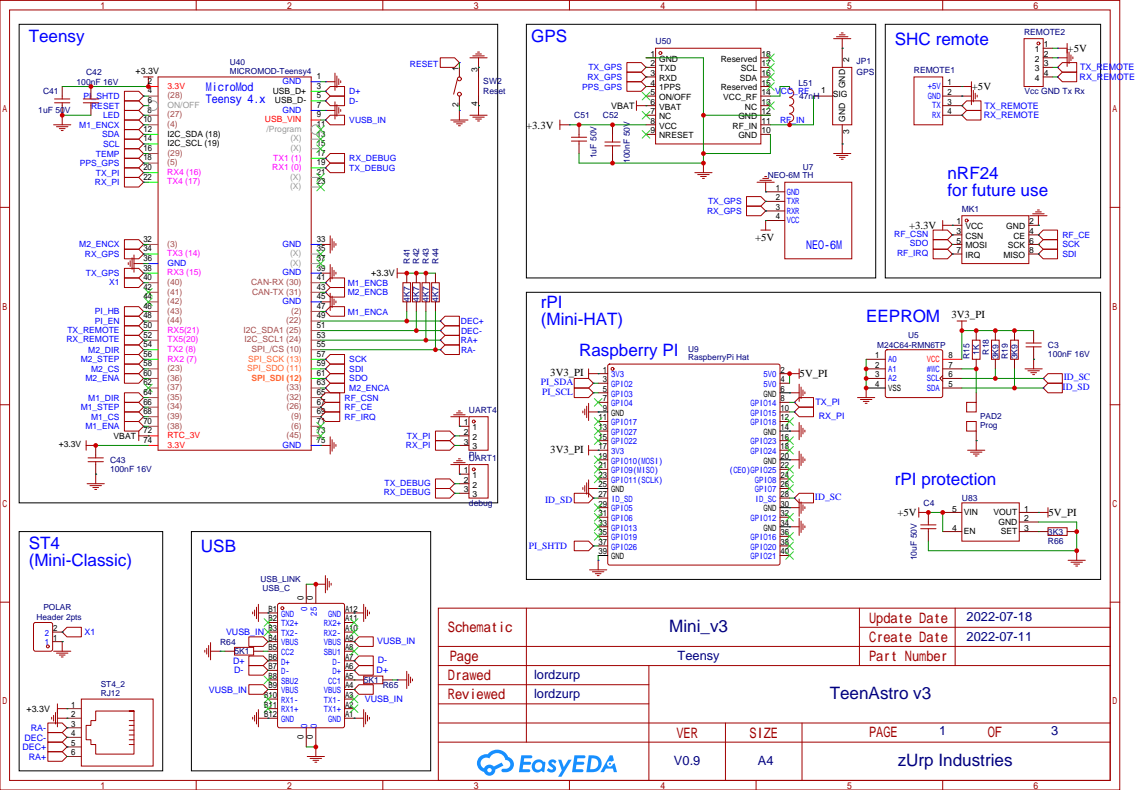
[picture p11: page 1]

# Power reverse protection

# ESD protection

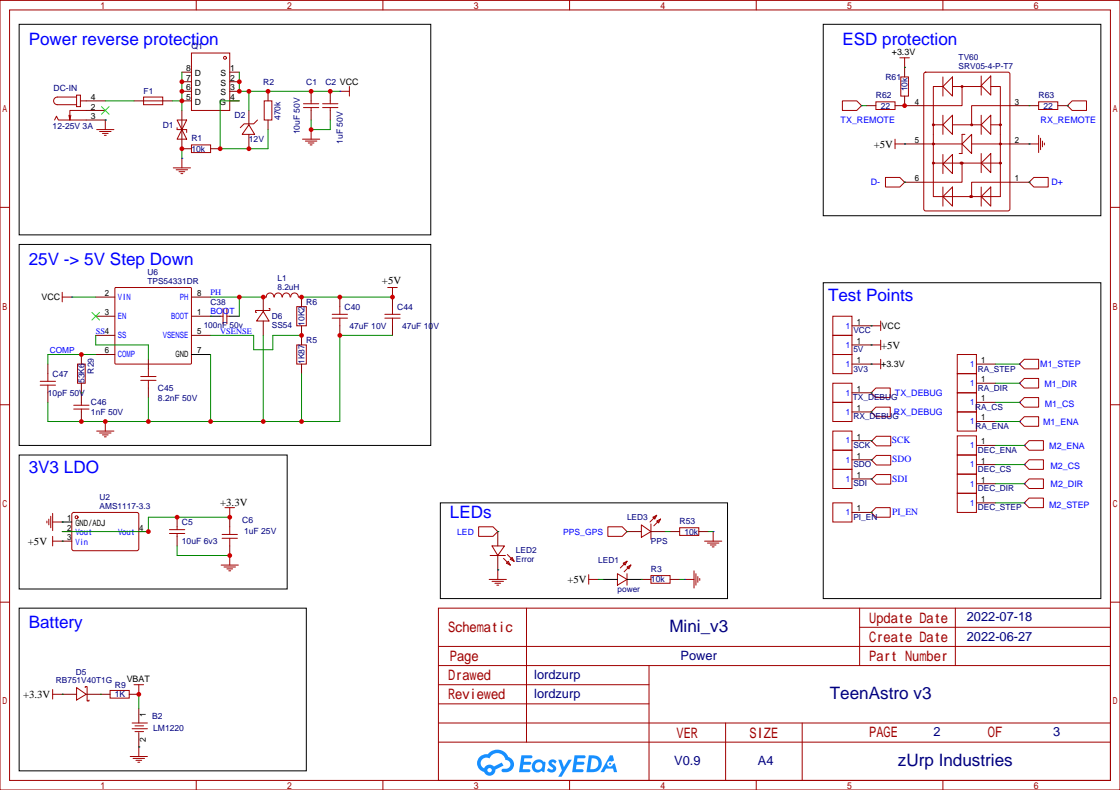
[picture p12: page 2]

Motor 1 (RA/ AZ) | Motor 2 (DEC / ALT)

# Motors connectors

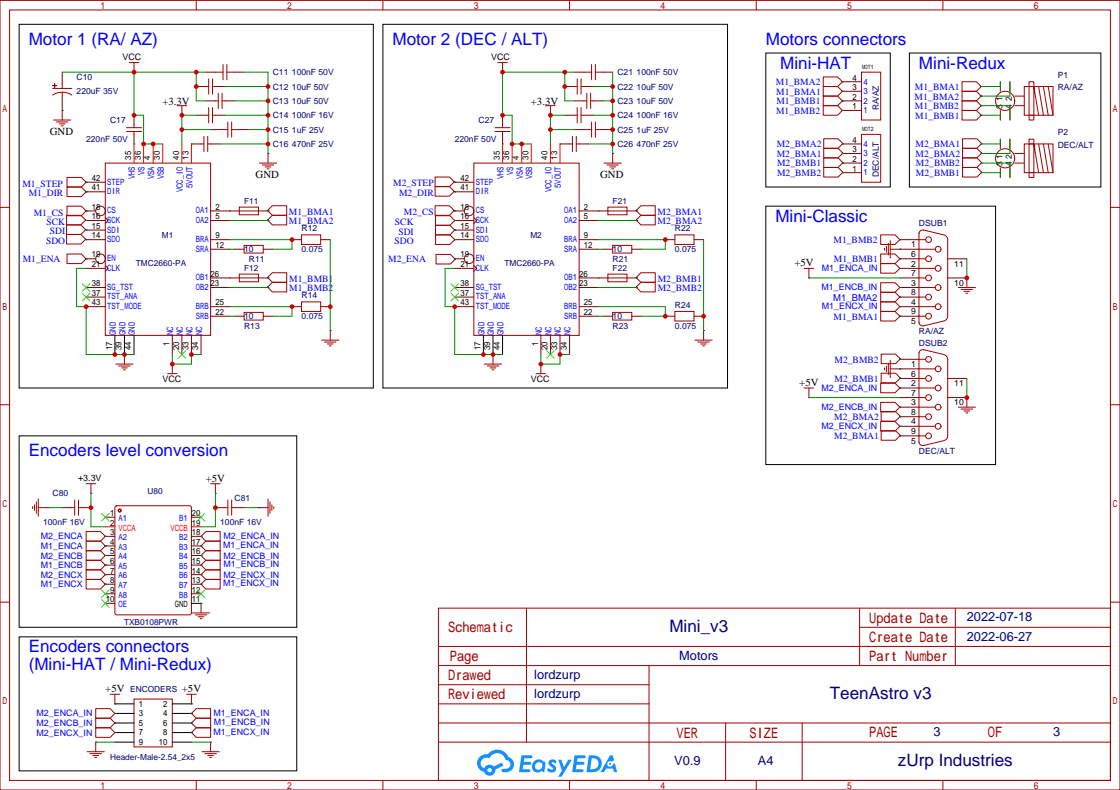
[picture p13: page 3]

Encoders connectors
(Mini-HAT / Mini-Redux)

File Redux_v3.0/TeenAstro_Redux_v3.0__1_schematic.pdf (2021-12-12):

+3.3V

## VCC

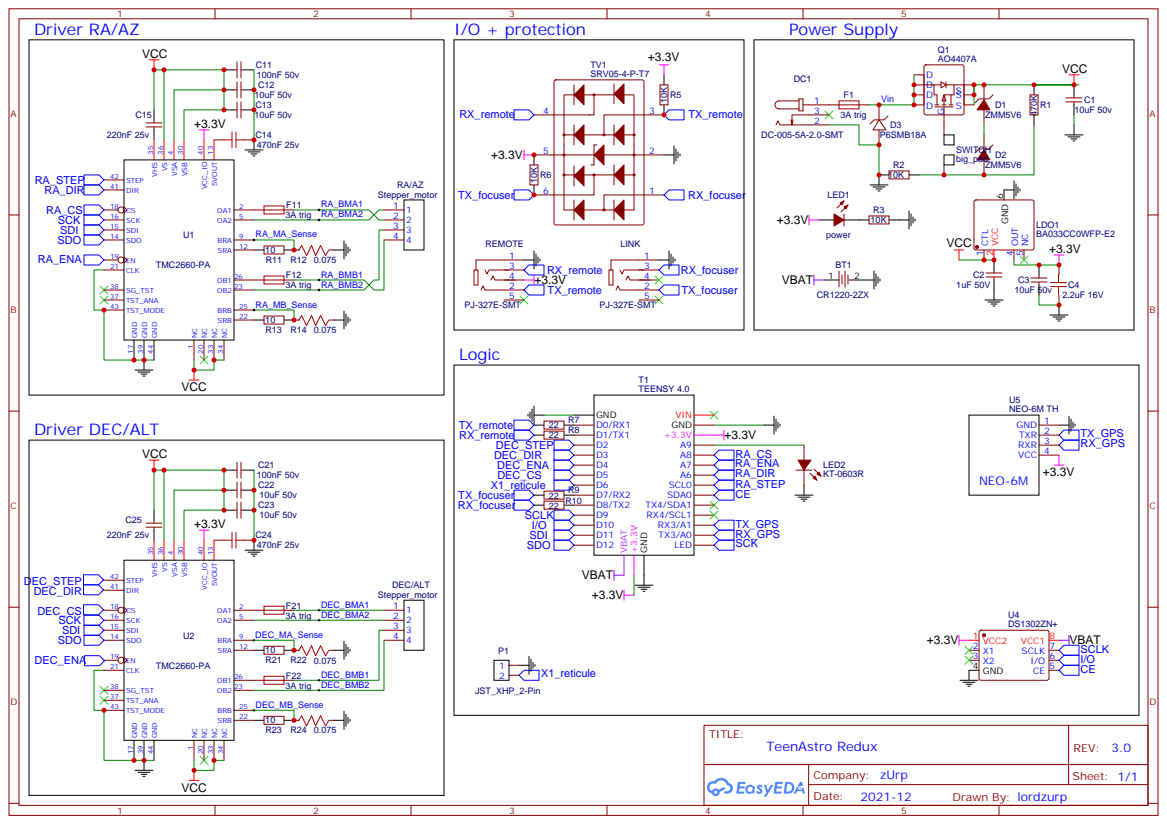
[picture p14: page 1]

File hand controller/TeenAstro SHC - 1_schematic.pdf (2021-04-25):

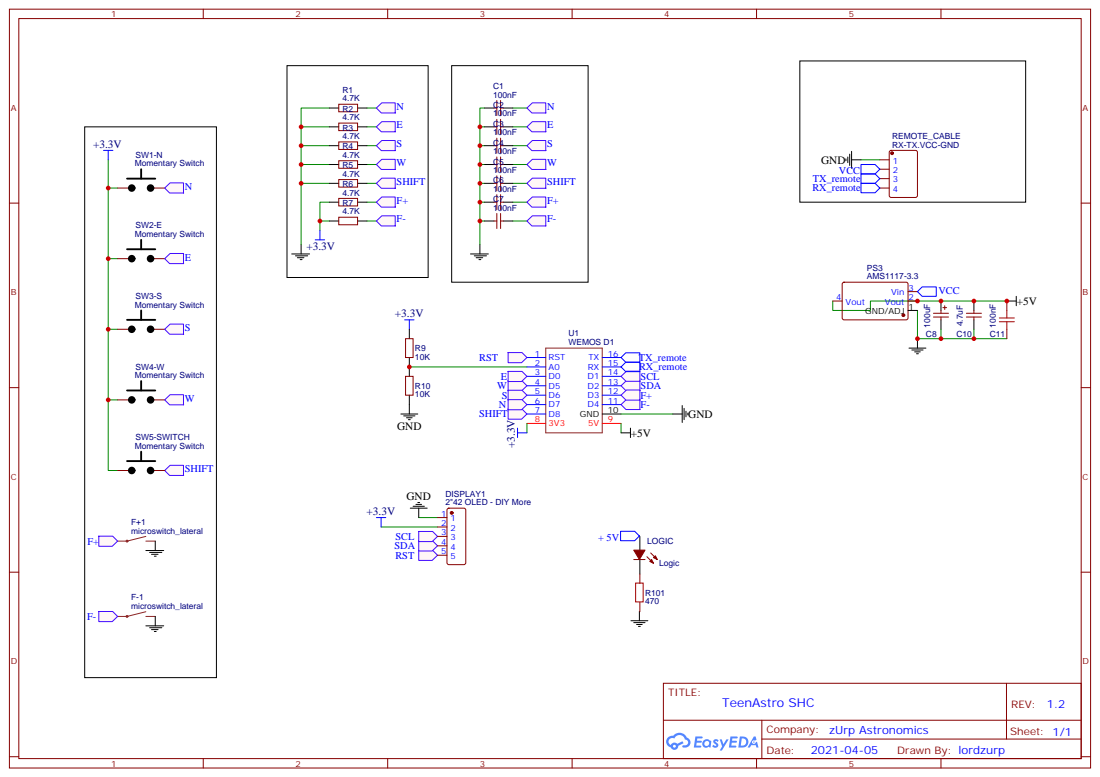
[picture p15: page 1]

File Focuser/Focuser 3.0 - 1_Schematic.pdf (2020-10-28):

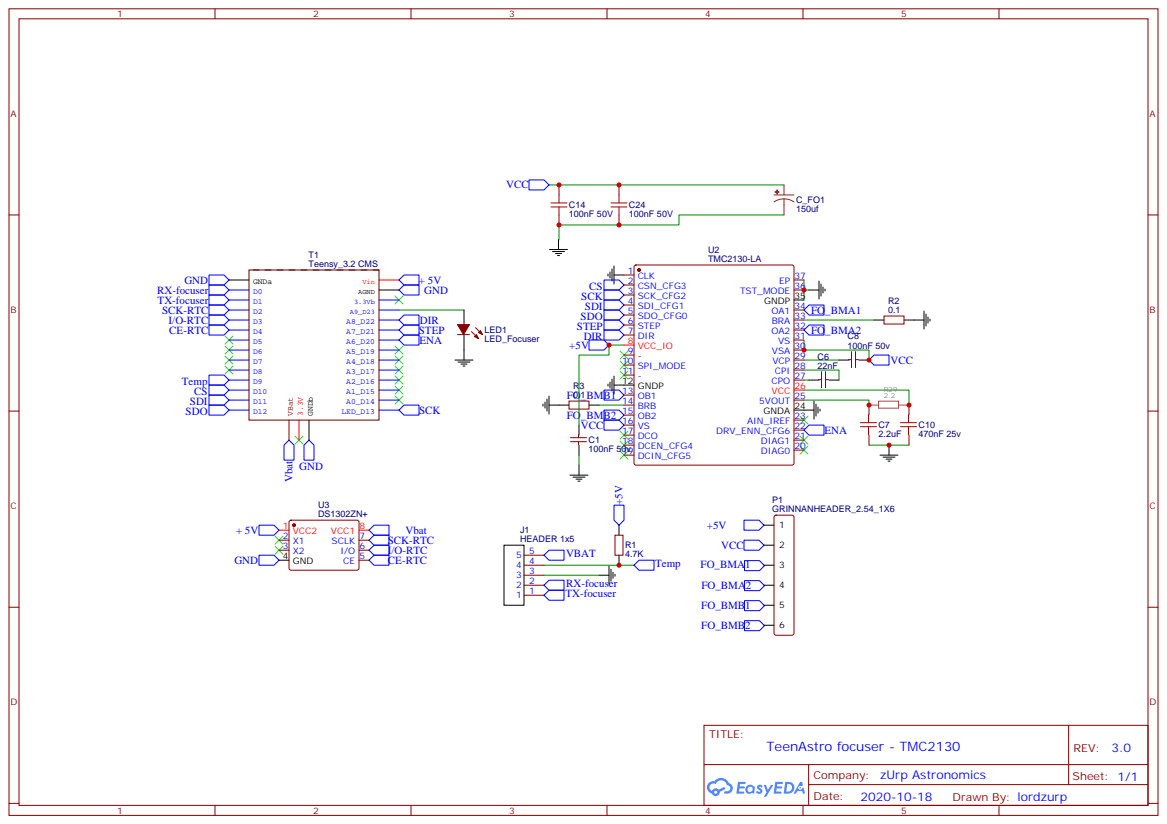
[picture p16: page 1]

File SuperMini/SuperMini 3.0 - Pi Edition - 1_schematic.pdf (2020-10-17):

## Focuser module

## NEO-6M

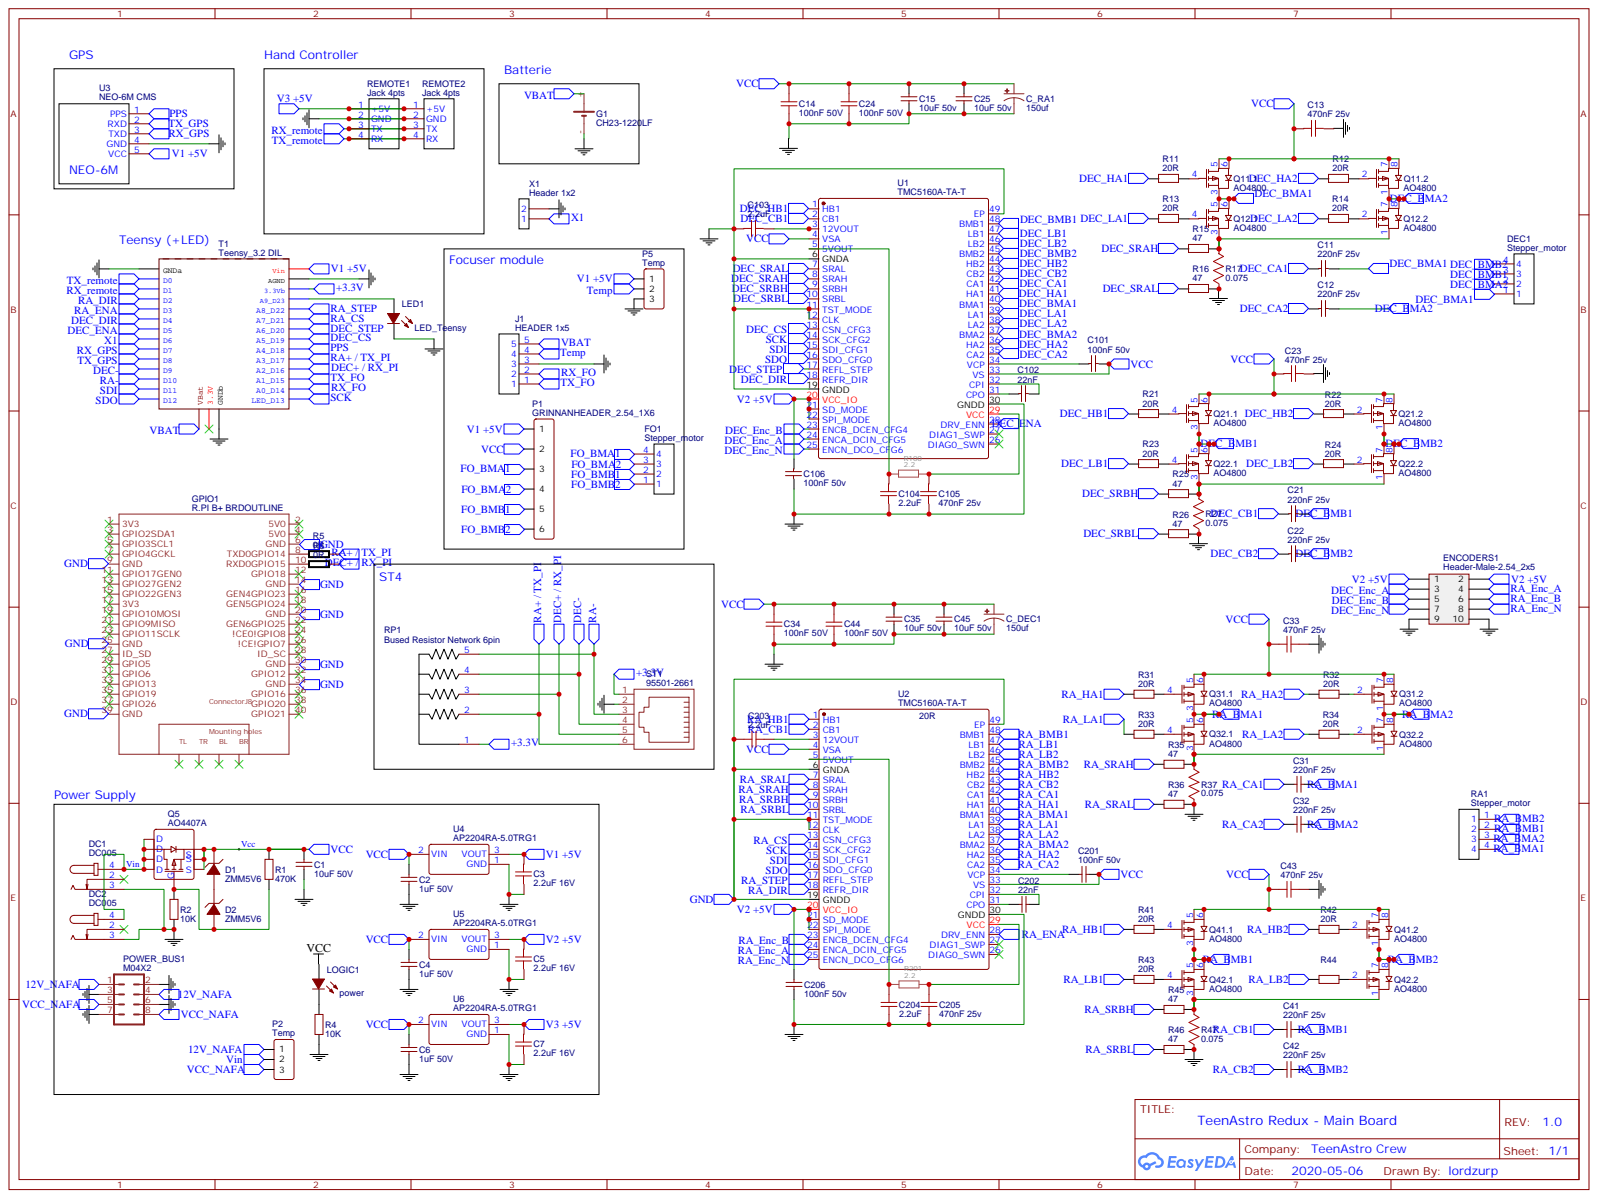
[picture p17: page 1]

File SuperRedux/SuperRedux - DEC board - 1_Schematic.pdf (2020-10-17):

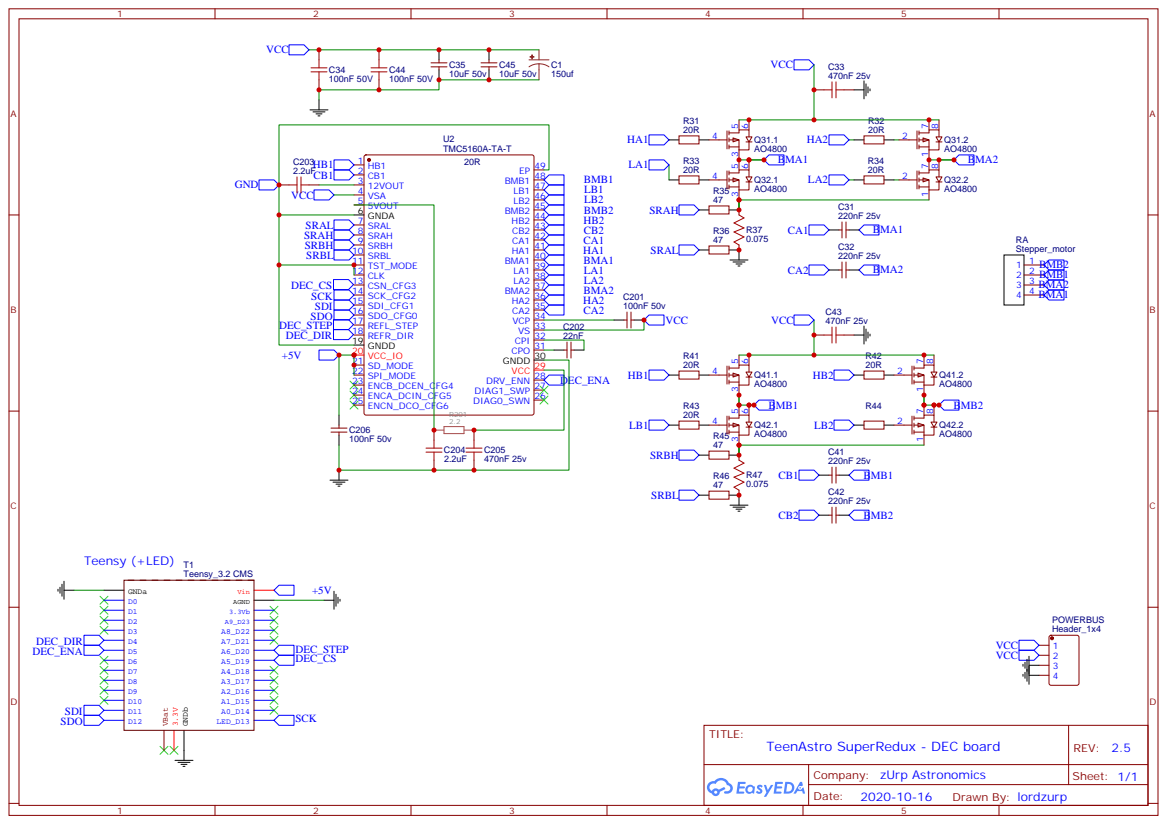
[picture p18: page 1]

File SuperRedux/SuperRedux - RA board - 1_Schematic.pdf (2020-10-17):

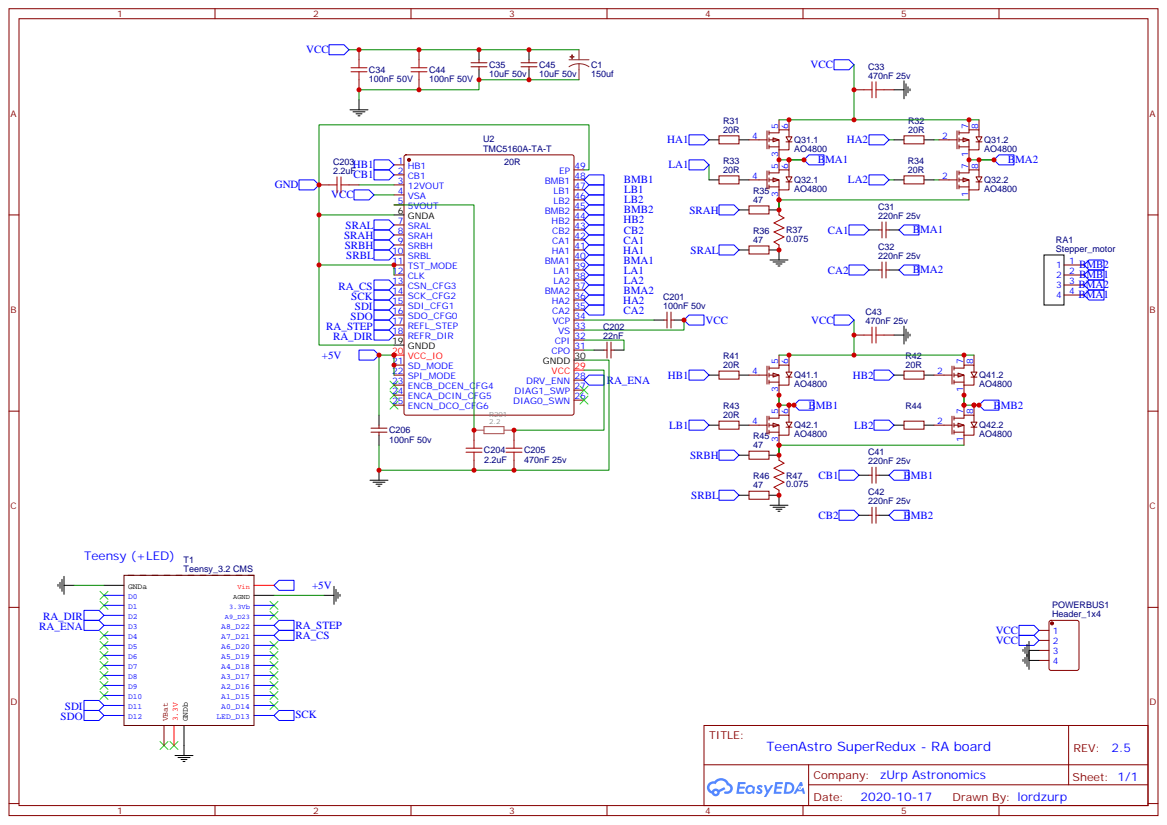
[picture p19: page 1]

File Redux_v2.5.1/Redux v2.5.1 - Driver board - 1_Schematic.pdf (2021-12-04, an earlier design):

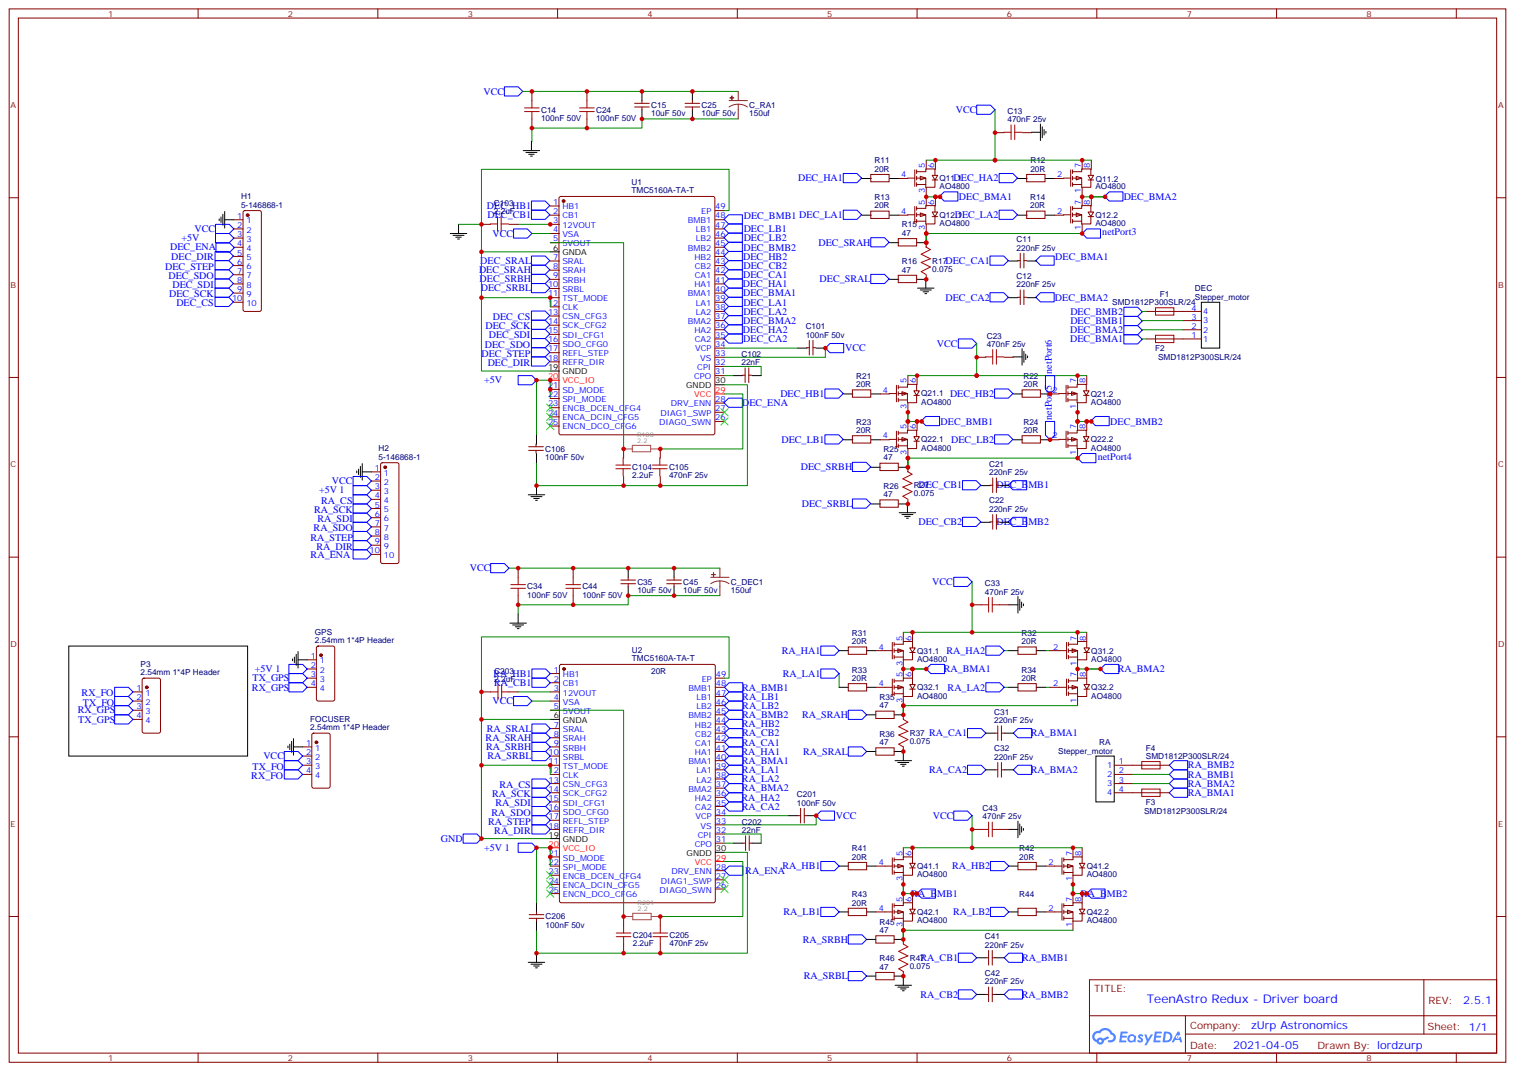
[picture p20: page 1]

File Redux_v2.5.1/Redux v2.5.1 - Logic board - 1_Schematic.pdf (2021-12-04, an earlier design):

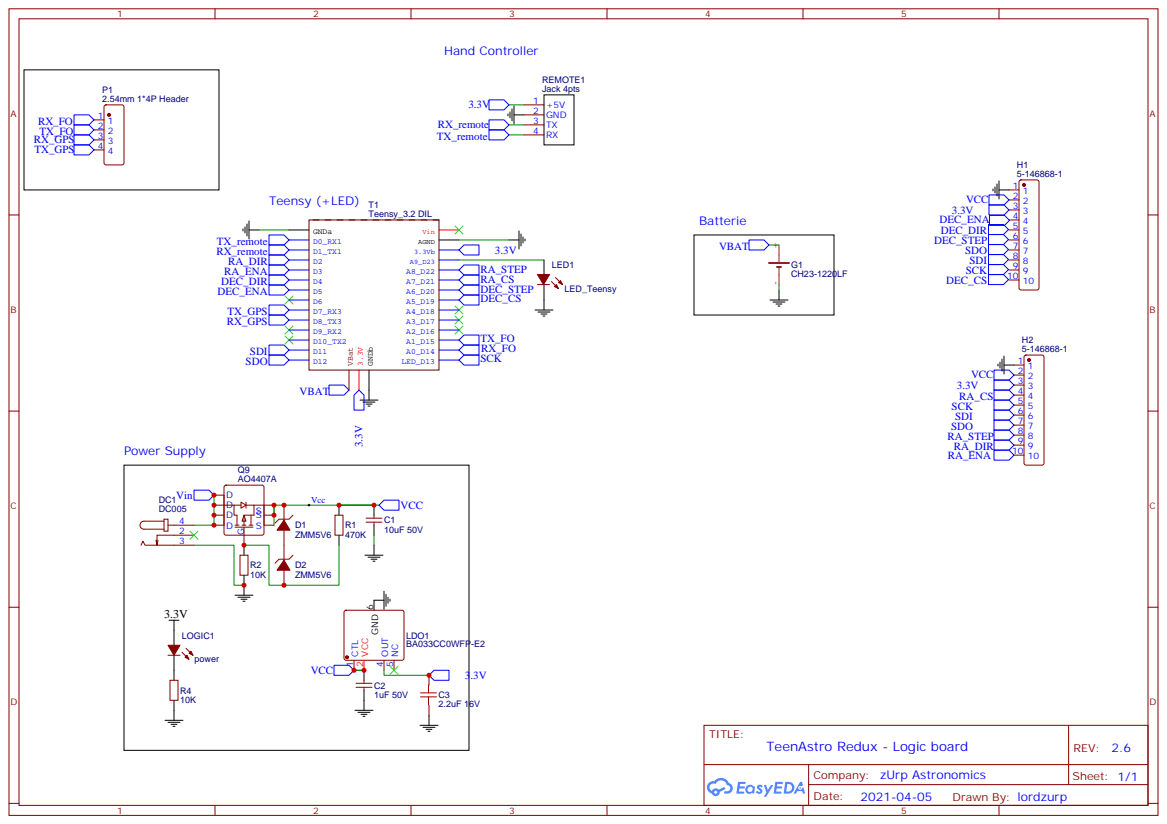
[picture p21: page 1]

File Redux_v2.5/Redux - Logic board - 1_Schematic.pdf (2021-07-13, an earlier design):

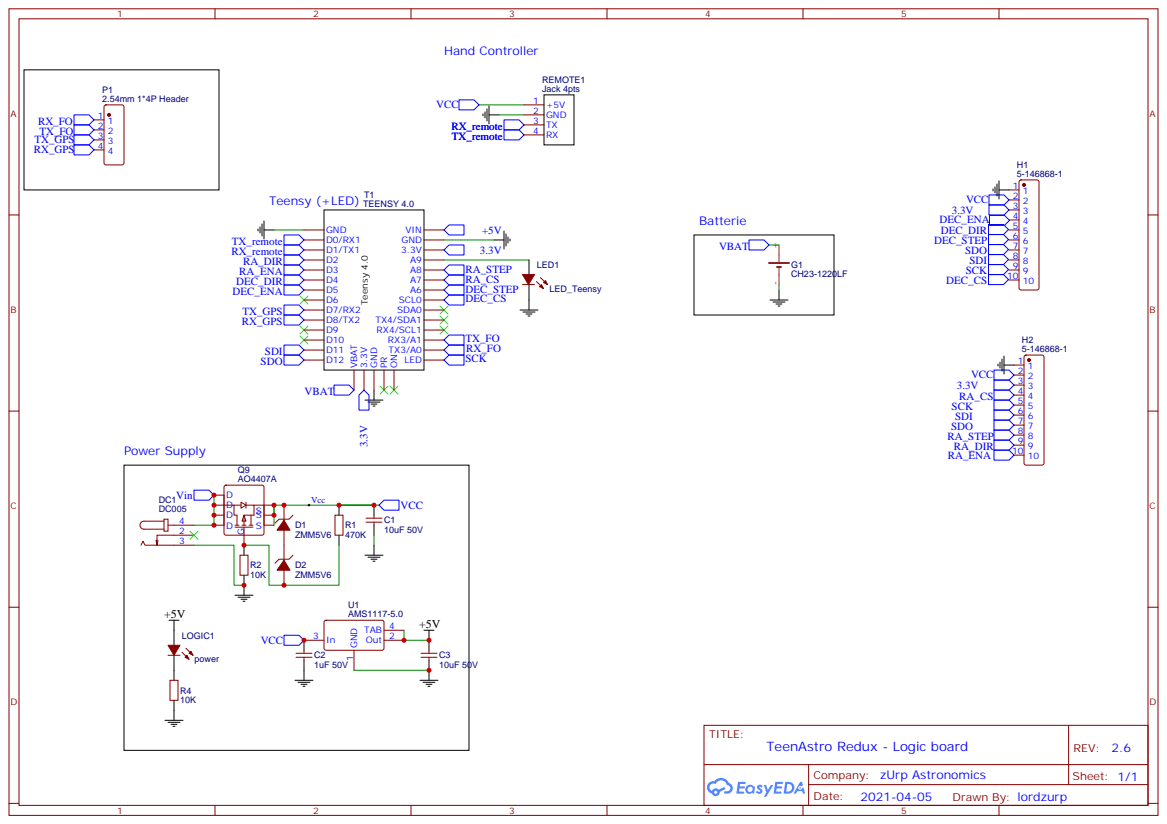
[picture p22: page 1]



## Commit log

2020-05-10 add schematics
2020-05-10 switch to GPL v3 license
2020-05-11 add productions files
    [BOM_TeenAstro_Redux-full.csv, PickAndPlace_TeenAstro_Redux-full.csv]
2020-05-11 prod files
    [Farnell_parts-list.csv]
2020-05-11 update part list
    [Farnell_parts-list.csv]
2020-10-17 v3.0 - PI Edition
    [BOM_PCB_2020-10-12_22-06-34_2020-10-12_22-13-28.csv, BOM_TeenAstro Redux - 2 Focuser TMC2130_2020-10-13_20-35-33.csv, BOM_TeenAstro Redux - 2 Focuser TMC2130_2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]
2020-10-28 clean PCB
    [Focuser 3.0 - 4_BOM.csv, Focuser 3.0 - 5_Pick n Place.csv, SuperMini 3.0 - Pi Edition - 4_BOM.csv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]
2020-10-30 placement ajusted
    [SuperMini 3.0 - Pi Edition - 5_Pick n Place.csv]
2020-10-30 focuser cleanup
    [Focuser 3.0 - 4_BOM.csv, Focuser 3.0 - 5_Pick n Place.csv]
2020-10-31 add wifi board (dirty preliminary)
2021-04-05 refresh project
    [BOM_SuperNES Hand Controller-D1flavour_2020-10-29_00-31-38.csv, BOM_SuperNES Hand Controller-D1flavour_2020-10-29_23-11-16.csv, BOM_SuperRedux - Driver board.c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]
2021-04-06 cleaning update to v1.1
    [TeenAstro SHC - 4_BOM.csv, TeenAstro SHC - 5_Pick n Place.csv]
2021-04-25 add LDO on remote
    [TeenAstro SHC - 4_BOM.csv]
2021-07-13 add firmware
    [Redux - Logic board - 4_BOM.csv, Redux - Logic board - 5_Pick n Place.csv]
2021-12-04 v2.5.1 push
    [BOM_TeenAstro-Redux_Driver-board_v3_2021-11-14.csv, PickAndPlace_PCB_TeenAstro-Redux_Driver-board_v3_2_2021-11-14.csv]
2021-12-11 v3 pre-release
    [BOM_TeenAstro-Redux_Driver-board_v3_2021-11-14.csv, PickAndPlace_PCB_TeenAstro-Redux_Driver-board_v3_2_2021-11-14.csv, Redux - Driver board - 4_BOM.csv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]
2022-06-06 v3.0 rebuild
    [BOM_TeenAstro-Redux_Driver-board_v3_2021-11-14.csv, Focuser 3.0 - 4_BOM.csv, Focuser 3.0 - 5_Pick n Place.csv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]
2022-06-25 grand ménage
    [Sheet_1_2022-06-06.schdoc, TeenAstro_ZH-1_2022-06-06.pcbdoc, TeenAstro_v3.0_ZH-1.PrjPcb]
2022-06-26 update schematics
2022-06-26 update prez.md (schematic)
2022-06-26 update schematic link (typo)
2022-06-26 add single sheet schematic
2022-06-26 add schematic link in prez.md
2022-06-26 single sheet schematic update
2022-06-26 precisions sur les GPIO
2022-06-26 add photo prototypes
2022-07-12 ajout datasheet
    [3D_TMC2660_BOB_V1.2.step, BOM_Mini Classic_TeenAstro v3.0_2022-07-04.xlsx, BOM_MiniHAT_TeenAstro v3.0_2022-07-05.xlsx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]
2022-07-14 clean folders
    [BOM_PCB_2020-10-12_22-06-34_2020-10-12_22-13-28.csv, BOM_SuperRedux - Driver board.csv, BOM_SuperRedux - logic board.csv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]
2022-07-18 on clean + mini-classic
    [BOM_Mini Classic_TeenAstro v3.0_2022-07-04.xlsx, BOM_MiniHAT_TeenAstro v3.0_2022-07-05.xlsx, BOM_TeenAstro_v3.0_HAT.xlsx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]
2022-07-18 nettoyage des liens
2022-07-18 màj bom
2022-12-18 v2.6 pre-release
    [TeenAstro_v2.6-Redux_4_BOM.xlsx, TeenAstro_v2.6-Redux_5_Pick_n_Place.xlsx, TeenAstro_v3.0-Mini-Classic_4_BOM.xlsx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]
2022-12-26 RC2 PowerDelivery
    [3D_TMC2660_BOB_V1.2.step, TeenAstro_v2.6-Redux_4_BOM.xlsx, TeenAstro_v2.6-Redux_5_Pick_n_Place.xlsx]
2022-12-30 v2.6.1 - pre release
    [TeenAstro_v2.6.1_Redux-DC_4_BOM.xlsx, TeenAstro_v2.6.1_Redux-DC_5_Pick_n_Place.xlsx, TeenAstro_v2.6.1_Redux-PD_4_BOM.xlsx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]
2024-06-01 clean repo
    [3D_TMC2660_BOB_V1.2.step, BOM_TMC2660_BOB_V1.2.xls, TeenAstro_v2.6-Redux_4_BOM.xlsx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]

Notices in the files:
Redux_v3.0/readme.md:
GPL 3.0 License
